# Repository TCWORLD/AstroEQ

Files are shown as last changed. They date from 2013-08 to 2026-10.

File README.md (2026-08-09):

*Last Updated: 8th Aug 2026*

# AstroEQ Telescope Mount Controller

### About The AstroEQ Project

AstroEQ was written and designed by Thomas Carpenter. Assistance with EQMOD and the Skywatcher Protocol was provided by Chris over at the EQMOD Yahoo group.

AstroEQ was primarily designed as an alternative to the SynScan upgrade for Skywatcher telescopes so that I could convert my non-GoTo mount into a full GoTo. Being a EE student at the time I decided to built my own controller rather than buying a commercial one. 

The primary goal of the project was to act as a gateway to connect the excellent EQMOD software (and hence ASCOM planetariums) to a motorised Equatorial mount that previously lacked Goto functionality.

The resulting design allows for almost any equatorial telescope mount which has bipolar stepper motors fitted to the RA and DEC axes to be connected to a PC and controlled via EQMOD.

The AstroEQ code contains a custom developed protocol decoder which uses the same Skywatcher protocol for communication that many Skywatcher go-to mounts use, and the same protocol which EQMOD was developed around. This allows it to be connected to EQMOD without any modification to that software regardless of what type of mount it is.

### Versions

The current software and hardware versions are as follows:

 * Config Utility Version: **3.9.3**
 * Firmware Verison: **8.25**
 * Hardware Version: **4.6/4.7 - see note below**

The AstroEQ configuration utility and precompiled firmware can be downloaded from either the Downloads folder, or the AstroEQ website at: https://astroeq.co.uk/download
Full version history can also be found on the AstroEQ downloads page.

The configuration utility is designed to run natively on Windows or Debian (e.g. Raspian/Ubuntu). You only need to run this utility when programming the mount.

I recommend people use the V4.6 design for DIY controllers.

The new V4.7 hardware design is functionality equivalent to the V4.6 design, but uses a mixture of PTH and SMD components to make it compatible with machine assembly.

### Making your own AstroEQ 

There are two hardware options:

 * Use an Arduino Mega (Uno is not supported), which requires only two DRV8825 or A4988 driver boards and a few passive components to build.
 * Use a completely custom hardware desgin which is based around an Atmega162 chip. Although this is not officially supported by the Arduino IDE, I have modified the bootloader to suit.

Further information can be found at https://astroeq.co.uk/buildown

### Help and Support

If you have any questions or need support, I have opened an AstroEQ Forum which can be found at https://astroeq.co.uk/forum/

The AstroEQ Firmware is currently proving to be very stable. If you do happen across any glitches, let me know as I can usually fix them fairly quickly.

### Required Software

Ascom can be downloaded from their website at: http://ascom-standards.org/ 

The EQMOD Project can be found at: http://eq-mod.sourceforge.net/

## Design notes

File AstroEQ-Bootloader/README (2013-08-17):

If you are building an AstroEQ from scratch, a special bootloader has to be programmed to the Atmega162 IC in order for the configuration utility to be able download the lastest version of the firmware and configure the mount.

The bootloader HEX file is included in this folder.

If you have bought a Kit or ready assembled AstroEQ board directly from me, the bootloader has already been installed. You can skip this step and move on to the config utility.
If you are using an Arduino Mega board, you can also skip this step as they already have a compatible bootloader installed.
If neither of the above apply, please read on...

You will need to connect your programmer to the ISP pins which are shown in the schematic (The ISP header)
You will then need to the software that came with your programmer to download the hex file and set the fuses.

The following fuse settings should be used:

High Fuse: 0xDC
Low Fuse: 0xFF
Extended Fuse*: 0xFB   
(*If you programmer flags up an error on the extended fuse, use 0x1A instead)

I use 'avrdude' to program hex files. You can find a good tutorial for that here: http://www.ladyada.net/learn/avr/avrdude.html

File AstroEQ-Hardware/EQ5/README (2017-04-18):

This is an experimental design I am using for my mount.

It is designed to fit within the shell of a Skywatcher EQ5, though takes a bit of work to install it.

I don't recommend using this design. It is provided as-is without any support.

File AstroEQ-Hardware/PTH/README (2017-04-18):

This folder contains designs used in purchased AstroEQ controllers and PCBs.

Currently V4.6 is the bare PCB version that I sell through the AstroEQ website. It is an easy to solder through-hole board. The Gerber files, Schematic and BOM, as well as the Eagle design files are all available in this folder.

V4.7 is a new part-SMD design that I will be using for the next run of controllers. I have made this switch to allow for machine assembly of the design. I would not recommend building this board yourself as it is functionally identical to the V4.6 board but will not be easy to assemble!

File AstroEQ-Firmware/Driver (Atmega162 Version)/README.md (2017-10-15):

### For Windows 10 Users

Installation of this driver is not necessary.

Windows 10 comes with a compatible driver preinstalled so it should automatically detect and install the necessary driver.

### For Window Vista/7/8.1 Users

Running DPInst_x86 or DPInst_x64 will install the AstroEQ driver (Use _x86 for 32bit OS, or _x64 for 64bit OS).
Alternatively you can install via Device Manager

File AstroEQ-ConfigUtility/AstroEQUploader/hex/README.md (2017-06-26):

Insert latest firmware .hex files here before running.

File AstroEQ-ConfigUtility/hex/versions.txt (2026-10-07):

AstroEQUploaderUtility	3.93
AstroEQV4-DIYBoard(includingKits)	8.29	AstroEQ V4-DIY Board (including DIY)	atmega162	arduino	57600
AstroEQArduinoMega2560	8.29	AstroEQ Arduino Mega 2560	atmega2560	wiring	115200
AstroEQArduinoMega1280	8.29	AstroEQ Arduino Mega 1280	atmega1280	arduino	57600
AstroEQV4-EQ5Board	8.29	AstroEQ V4-EQ5 Board	atmega162	arduino	57600
AstroEQRamps14Mega2560	8.29	AstroEQ Ramps 1.4 w/ Mega 2560	atmega2560	wiring	115200

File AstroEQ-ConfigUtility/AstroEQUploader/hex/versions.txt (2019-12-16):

AstroEQUploaderUtility	3.91
AstroEQV4-DIYBoard(includingKits)	8.16	AstroEQ V4-DIY Board (including DIY)	atmega162	arduino	57600
AstroEQArduinoMega2560	8.16	AstroEQ Arduino Mega 2560	atmega2560	wiring	115200
AstroEQArduinoMega1280	8.16	AstroEQ Arduino Mega 1280	atmega1280	arduino	57600
AstroEQV4-EQ5Board	8.16	AstroEQ V4-EQ5 Board	atmega162	arduino	57600
AstroEQRamps14Mega2560	8.16	AstroEQ Ramps 1.4 w/ Mega 2560	atmega2560	wiring	115200

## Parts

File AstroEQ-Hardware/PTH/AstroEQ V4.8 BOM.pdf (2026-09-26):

Qty | Parts | Value | Description | Manufacturer | Part Number | Farnell Code
| 2 SJ1, SJ2 | - | Solder Jumper - See PCB for details | - | - | -
| 7 C1, C3, C5, C9, C10, C11, C15 | 100nF | 100nF Ceramic Capacitor, 50V, 2.54mm pitch | MULTICOMP | MCRR25104X7RK0050 | 1216438
| 3 C2, C4, C12 | 100uF | 100uF Alu Electrolytic Capacitor, 25V, Dia 6.3mm | MULTICOMP | MCGPR25V107M6.3X11 | 9451188
| 4 C7, C8, C13, C14 | 22pF | 22pF Ceramic Capacitor, 2.54mm pitch | AVX | SR151A220JAR | 1100369
| 1 D1 | MBR1060 | TO-220 Schottky Diode, 10A | MULTICOMP | MBR1060 | 1625119
| 1 ST4 | RJ11-6 | RJ11 JACK, 6/6 LOW PROFILE | MOLEX | 95501-2661 | 1536490
| 2 DEC, RA | RJ11-4 | RJ11 JACK, 6/4 LOW PROFILE | MOLEX | 95501-2641 | 1560166
| 1 HAMMOND-1593N | HAMMOND-1593N | CASE, ABS, HANDHELD, BLACK, 111X75X25MM | HAMMOND | 1593NBK | 9287566
| 1 IC1 | ATMEGA162-16PU | IC, ATMEGA162-16PU, DIP40 | ATMEL | ATMEGA162-16PU | 9171169
| 1 IC1 | DIP40 Socket | 40Way DIP IC Socket, 0.3" Pitch | MULTICOMP | 2227-20-03-07 | 4285608
| 1 IC2 | PIC18F14K50-I/P | IC, PIC18F14K50-I/P, PDIP20 | MICROCHIP | PIC18F14K50-I/P | 1648501
| 1 IC2 | DIP20 Socket | 40Way DIP IC Socket, 0.6" Pitch | MULTICOMP | 2227-40-06-05 | 4285669
| 1 IC3 | 78L05 | 5V 100mA Voltage Regulator, TO-92 | FAIRCHILD SEMICONDUCTOR | LM78L05ACZX | 1467367
| 1 J1 | MJ-179PH | DC Barrel Jack Socket, PCB Mount | MULTICOMP | MJ-179PH | 1737246
| 2 M1, M2 | Motor Driver Socket | RECEPTACLE, 2.54MM, SINGLE, 16WAY | SAMTEC | CES-116-01-T-S | 1667522
| 1 PROG | 2x3 Header | 2ROW, 6WAY, 2.54mm Pitch Header | TE CONNECTIVITY / AMP | 826632-3 | 3418492
7 R13, R14, R15, R16, R19, R21, R23 1kR | 1k Resistor, 1/4W, 5% | MULTICOMP | MF12 1K | 9342400
| 1 USB-> | Mini USB Connector | MINI USB RECEPTACLE, THT, R/A | MOLEX | 565790519 | 1125347
| 1 X2 | 12MHz XTAL | XTAL, 12.000MHZ, 18PF, HC-49S | TXC | 9B-12.000MAAJ-B | 1842203
| 3 R1, R18, R20 | 10kR | 10k Resistor, 1/4W, 5% | MULTICOMP | MF12 10K | 9342419
| 3 PWR, STAT, USB | 3mm LED Red | Flat Top Red LED, 3mm | KINGBRIGHT | L-424HDT | 1142499
| 1 X1 | 16MHz XTAL | XTAL, 16.000MHZ, 18PF, HC-49S | TXC | 9B-16.000MEEJ-B | 1842217
| 1 D2 | 1N4148 | DIODE, 100V,150MA, DO-35 | MULTICOMP | 1N4148 | 9565124
| 1 C6 | 470nF | 470nF Ceramic Capacitor, 50V, 2.54mm pitch | KEMET | C320C474M5U5T
| | | | | A | 1457660
| 1 R22 | 120R | 120R Resistor, 1/4W, 5
| | | % | MULTICOMP | MF12 120R | 9342516
| 1 Q1 | BS270 | MOSFET TRANSISTOR, N CHANNEL, BS270 | FAIRCHILD SEMICONDUCTOR | BS270 | 1017689
| 1 PWM | 3.5mm JACK | PHONE AUDIO CONNECTOR, JACK, 3.5MM | CLIFF ELECTRONIC COMPONENETS | FC68131 | 2518188
1 Pack | - | Mounting PCB to Case | WASHER, FLAT, NYLON, M2.5, PK50 | DURATOOL | 110764 | 7047472
1 Pack | - | Mounting PCB to Case | SCREW, POZI PAN, STEEL, BZP, M2.5X6 | TR FASTENINGS | M2.56 PRSTTTZ100 | 1420119

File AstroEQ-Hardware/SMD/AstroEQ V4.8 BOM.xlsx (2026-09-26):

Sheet: Summary
Number of installed components | 47
Number of different components | 24
Number of BGAs per circuit | 0
Number of QFNs per circuit | 0

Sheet: Parts List Summary
Line No | Part Name | Part Number/Value | Quantity Per Board | REF DES | Notes | Manufacturer | P/N | Supplier | Order Code
1 | POWER_JACKPTH | POWER_JACKPTH | 1 | 12V | . | MULTICOMP | MJ-179PH | Farnell | 1737246
2 | C-EUC0603 | 100n 0603 50V 10% X7R | 7 | C1, C3, C5, C9, C10, C11, C15 | . | MULTICOMP | MC0603B104K500CT | Farnell | 1759122
3 | CPOL-EUD | 100u 0.38R 35V 20% ALU-ELEC | 3 | C2, C4, C12 | . | Wurth Elektronik | 865080545012 | Mouser | 710-865080545012
4 | C-EUC0603 | 470n 0603 16V 10% X5R | 1 | C6 | . | MULTICOMP | MC0603X474K160CT | Farnell | 1759405
5 | C-EUC0603 | 22p 0603 50V 5% C0G/NP0 | 4 | C7, C8, C13, C14 | . | MULTICOMP | MC0603N220J500CT | Farnell | 1759057
6 | DIODE-SMC | B550C-13 SMC | 1 | D1 | . | DIODES INC. | B550C-13-F | Farnell | 1858608
7 | DIODESOD | RB511VM-30FHTE-17 SOD-323 | 1 | D2 | . | ROHM | RB511VM-30FHTE-17 | Farnell | 2581544
8 | RJ11-4-LP | RJ11-4-LP | 2 | DEC, RA | . | Molex | 95501-2641 | Farnell | 1560166
9 | DIP40 | DIP40-SOCKET | 1 | IC1 | . | 3M | 4840-6000-CP | Mouser | 517-4840-6000-CP
10 | DIP20 | DIP20-SOCKET | 1 | IC2 | . | MULTICOMP | 2227-20-03-07 | Farnell | 4285608
11 | V_REG_78XX-SOT89 | 78L05 SOT89 | 1 | IC3 | . | STMicroelectronics | L78L05ACUTR | Farnell | 1366573
12 | LED-1206-SIDE | Red | 3 | LINK, PWR, STAT | . | Wurth Elektronik | 155124RS73200 | Farnell | 2322101
13 | A4983-DUAL-HV | Motor Driver | 2 | M1, M2 | . | Samtec | CES-116-01-T-S | Farnell | 1667522
14 | 2x3-Pin Header | AVR_PRG | 1 | PROG | . | Harwin | M20-9980346 | Farnell | 1022231
15 | AUDIO-JACKPTH | JACK | 1 | PWM | . | CLIFF Electronic Components | FC68131 | Farnell | 2518188
16 | MOSFET-NCHANNELSMD | NTR4501NT1G SOT23 | 1 | Q1 | . | ONSemiconductor | NTR4501NT1G | Farnell | 1431305
17 | R-EU_R0603 | 10k 0603 1% 0.063W | 3 | R1, R18, R20 | . | MULTICOMP | MC0063W0603110K | Farnell | 2130939
18 | R-EU_R0603 | 1k 0603 1% 0.063W | 7 | R13, R14, R15, R16, R19, R21, R23 | . | MULTICOMP | MC0063W060311K | Farnell | 2130855
19 | R-EU_R0805 | 120R 0805 1% 0.1W | 1 | R22 | . | MULTICOMP | MC01W08051120R | Farnell | 2129039
20 | 1x3-Pin Header | 3pin HDR | 2 | SJ1, SJ2 | . | Harwin | M20-9990345 | Farnell | 1022248
21 | RJ11-LP | RJ11-6 | 1 | ST4 | . | Molex | 95501-2661 | Farnell | 1536490
22 | USBMINIAB | Molex 67803-8020 | 1 | USB | . | Molex | 67803-8020 | Farnell | 1355761
23 | XTALNX5032 | 16MHz 5x3.2 20ppm | 1 | X1 | . | ABRACON | ABM3-16.000MHZ-D2Y-T | Mouser | 815-ABM3-16-D2Y-T
24 | XTALNX5032 | 12MHz 5x3.2 30ppm | 1 | X2 | . | TXC | 7A-12.000MAAJ-T | Farnell | 1841940
 |  |  |  |  | .
 |  |  |  |  | .
 |  |  |  |  | .
 |  |  |  |  | .
 |  |  |  |  | .
 |  |  |  |  | .
 |  |  |  |  | .
 |  |  |  |  | .
 |  |  |  |  | .
 |  |  |  |  | .
 |  |  |  |  | .
 |  |  |  |  | .
 |  |  |  |  | .
 |  |  |  |  | .
 |  |  |  |  | .
 |  |  |  |  | .
 |  |  |  |  | .
 |  |  |  |  | .
 |  |  |  |  | .
 |  |  |  |  | .
 |  |  |  |  | .
 |  |  |  |  | .
 |  |  |  |  | .
 |  |  |  |  | .
 |  |  |  |  | .
 |  |  |  |  | .
 |  |  |  |  | .
 |  |  |  |  | .
 |  |  |  |  | .
 |  |  |  |  | .
 |  |  |  |  | .
 |  |  |  |  | .
 |  |  |  |  | .
 |  |  |  |  | .
 |  |  |  |  | .
 |  |  |  |  | .
 |  |  |  |  | .
 |  |  |  |  | .
 |  |  |  |  | .
 |  |  |  |  | .
 |  |  |  |  | .
 |  |  |  |  | .
 |  |  |  |  | .
 |  |  |  |  | .
 |  |  |  |  | .
 |  |  |  |  | .
 |  |  |  |  | .
 |  |  |  |  | .
 |  |  |  |  | .
 |  |  |  |  | .
 |  |  |  |  | .
 |  |  |  |  | .
 |  |  |  |  | .
 |  |  |  |  | .
 |  |  |  |  | .
 |  |  |  |  | .
 |  |  |  |  | .
 |  |  |  |  | .
 |  |  |  |  | .
 |  |  |  |  | .
 |  |  |  |  | .
 |  |  |  |  | .
 |  |  |  |  | .
 |  |  |  |  | .
 |  |  |  |  | .
 |  |  |  |  | .
 |  |  |  |  | .
 |  |  |  |  | .
 |  |  |  |  | .
 |  |  |  |  | .
 |  |  |  |  | .
 |  |  |  |  | .
 |  |  |  |  | .
 |  |  |  |  | .
 |  |  |  |  | .
 |  |  |  |  | .
 |  |  |  |  | .
 |  |  |  |  | .
 |  |  |  |  | .
 |  |  |  |  | .
 |  |  |  |  | .
 |  |  |  |  | .
 |  |  |  |  | .
 |  |  |  |  | .
 |  |  |  |  | .
 |  |  |  |  | .
 |  |  |  |  | .
 |  |  |  |  | .
 |  |  |  |  | .
 |  |  |  |  | .
 |  |  |  |  | .
 |  |  |  |  | .
 |  |  |  |  | .
 |  |  |  |  | .
 |  |  |  |  | .
 |  |  |  |  | .
 |  |  |  |  | .
 |  |  |  |  | .
 |  |  |  |  | .
 |  |  |  |  | .
 |  |  |  |  | .
 |  |  |  |  | .
 |  |  |  |  | .
 |  |  |  |  | .
 |  |  |  |  | .
 |  |  |  |  | .
 |  |  |  |  | .
 |  |  |  |  | .
 |  |  |  |  | .
 |  |  |  |  | .
 |  |  |  |  | .
 |  |  |  |  | .
 |  |  |  |  | .
 |  |  |  |  | .
 |  |  |  |  | .
 |  |  |  |  | .
 |  |  |  |  | .
 |  |  |  |  | .
 |  |  |  |  | .
 |  |  |  |  | .
 |  |  |  |  | .
 |  |  |  |  | .
 |  |  |  |  | .
 |  |  |  |  | .
 |  |  |  |  | .
 |  |  |  |  | .
 |  |  |  |  | .
 |  |  |  |  | .
 |  |  |  |  | .
 |  |  |  |  | .
 |  |  |  |  | .
 |  |  |  |  | .
 |  |  |  |  | .
 |  |  |  |  | .
 |  |  |  |  | .
 |  |  |  |  | .
 |  |  |  |  | .
 |  |  |  |  | .
 |  |  |  |  | .
 |  |  |  |  | .
 |  |  |  |  | .
 |  |  |  |  | .
 |  |  |  |  | .
 |  |  |  |  | .
 |  |  |  |  | .
 |  |  |  |  | .
 |  |  |  |  | .
 |  |  |  |  | .
 |  |  |  |  | .
 |  |  |  |  | .
 |  |  |  |  | .
 |  |  |  |  | .
 |  |  |  |  | .
 |  |  |  |  | .
 |  |  |  |  | .
 |  |  |  |  | .
 |  |  |  |  | .
 |  |  |  |  | .
 |  |  |  |  | .
 |  |  |  |  | .
 |  |  |  |  | .
 |  |  |  |  | .
 |  |  |  |  | .
 |  |  |  |  | .
 |  |  |  |  | .
 |  |  |  |  | .
 |  |  |  |  | .
 |  |  |  |  | .
 |  |  |  |  | .
 |  |  |  |  | .
 |  |  |  |  | .
 |  |  |  |  | .
 |  |  |  |  | .
 |  |  |  |  | .
 |  |  |  |  | .
 |  |  |  |  | .
 |  |  |  |  | .
 |  |  |  |  | .
 |  |  |  |  | .
 |  |  |  |  | .
 |  |  |  |  | .
 |  |  |  |  | .
 |  |  |  |  | .
 |  |  |  |  | .
 |  |  |  |  | .
 |  |  |  |  | .
 |  |  |  |  | .
 |  |  |  |  | .
 |  |  |  |  | .
 |  |  |  |  | .
 |  |  |  |  | .
 |  |  |  |  | .
 |  |  |  |  | .
 |  |  |  |  | .
 |  |  |  |  | .
 |  |  |  |  | .
 |  |  |  |  | .
 |  |  |  |  | .
 |  |  |  |  | .
 |  |  |  |  | .
 |  |  |  |  | .
 |  |  |  |  | .
 |  |  |  |  | .
 |  |  |  |  | .
 |  |  |  |  | .
 |  |  |  |  | .
 |  |  |  |  | .
 |  |  |  |  | .
 |  |  |  |  | .
 |  |  |  |  | .
 |  |  |  |  | .
 |  |  |  |  | .
 |  |  |  |  | .
 |  |  |  |  | .
 |  |  |  |  | .
 |  |  |  |  | .
 |  |  |  |  | .
 |  |  |  |  | .
 |  |  |  |  | .
 |  |  |  |  | .
 |  |  |  |  | .
 |  |  |  |  | .
 |  |  |  |  | .
 |  |  |  |  | .
 |  |  |  |  | .
 |  |  |  |  | .
 |  |  |  |  | .
 |  |  |  |  | .
 |  |  |  |  | .
 |  |  |  |  | .
 |  |  |  |  | .
 |  |  |  |  | .
 |  |  |  |  | .
 |  |  |  |  | .
 |  |  |  |  | .
 |  |  |  |  | .
 |  |  |  |  | .

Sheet: Master BOM
Ref Designator | Part Name | BOM Value | Rotation | X (thou) | Y (thou) | Side | Part ID | Line No | Install? | Is BGA | Is QFN | Manufacturer | Manufacturers P/N
12V | POWER_JACKPTH | POWER_JACKPTH | 270 | -2.22 | 47.31 | TOP | 40 | 1 | TRUE | FALSE | FALSE | MULTICOMP | MJ-179PH
C1 | C-EUC0603 | 100n 0603 50V 10% X7R | 270 | 80.01 | 15.24 | TOP | 13 | 2 | TRUE | FALSE | FALSE | MULTICOMP | MC0603B104K500CT
C3 | C-EUC0603 | 100n 0603 50V 10% X7R | 270 | 80.01 | 35.56 | TOP | 13 | 2 | TRUE | FALSE | FALSE | MULTICOMP | MC0603B104K500CT
C5 | C-EUC0603 | 100n 0603 50V 10% X7R | 180 | 17.46 | 14.29 | TOP | 13 | 2 | TRUE | FALSE | FALSE | MULTICOMP | MC0603B104K500CT
C9 | C-EUC0603 | 100n 0603 50V 10% X7R | 0 | 23.5 | 37.47 | TOP | 13 | 2 | TRUE | FALSE | FALSE | MULTICOMP | MC0603B104K500CT
C10 | C-EUC0603 | 100n 0603 50V 10% X7R | 180 | 11.11 | 64.45 | TOP | 13 | 2 | TRUE | FALSE | FALSE | MULTICOMP | MC0603B104K500CT
C11 | C-EUC0603 | 100n 0603 50V 10% X7R | 0 | 6.03 | 58.42 | TOP | 13 | 2 | TRUE | FALSE | FALSE | MULTICOMP | MC0603B104K500CT
C15 | C-EUC0603 | 100n 0603 50V 10% X7R | 180 | 26.67 | 3.81 | TOP | 13 | 2 | TRUE | FALSE | FALSE | MULTICOMP | MC0603B104K500CT
C2 | CPOL-EUD | 100u 0.38R 35V 20% ALU-ELEC | 90 | 82.87 | 29.85 | TOP | 15 | 3 | TRUE | FALSE | FALSE | Wurth Elektronik | 865080545012
C4 | CPOL-EUD | 100u 0.38R 35V 20% ALU-ELEC | 90 | 82.87 | 48.58 | TOP | 15 | 3 | TRUE | FALSE | FALSE | Wurth Elektronik | 865080545012
C12 | CPOL-EUD | 100u 0.38R 35V 20% ALU-ELEC | 180 | 18.73 | 51.12 | TOP | 15 | 3 | TRUE | FALSE | FALSE | Wurth Elektronik | 865080545012
C6 | C-EUC0603 | 470n 0603 16V 10% X5R | 0 | 9.21 | 25.08 | TOP | 14 | 4 | TRUE | FALSE | FALSE | MULTICOMP | MC0603X474K160CT
C7 | C-EUC0603 | 22p 0603 50V 5% C0G/NP0 | 270 | 24.77 | 9.53 | TOP | 12 | 5 | TRUE | FALSE | FALSE | MULTICOMP | MC0603N220J500CT
C8 | C-EUC0603 | 22p 0603 50V 5% C0G/NP0 | 270 | 20.32 | 9.53 | TOP | 12 | 5 | TRUE | FALSE | FALSE | MULTICOMP | MC0603N220J500CT
C13 | C-EUC0603 | 22p 0603 50V 5% C0G/NP0 | 0 | 53.66 | 47.31 | TOP | 12 | 5 | TRUE | FALSE | FALSE | MULTICOMP | MC0603N220J500CT
C14 | C-EUC0603 | 22p 0603 50V 5% C0G/NP0 | 0 | 53.66 | 44.13 | TOP | 12 | 5 | TRUE | FALSE | FALSE | MULTICOMP | MC0603N220J500CT
D1 | DIODE-SMC | B550C-13 SMC | 180 | 20.96 | 59.69 | TOP | 24 | 6 | TRUE | FALSE | FALSE | DIODES INC. | B550C-13-F
D2 | DIODESOD | RB511VM-30FHTE-17 SOD-323 | 180 | 9.21 | 22.86 | TOP | 23 | 7 | TRUE | FALSE | FALSE | ROHM | RB511VM-30FHTE-17
DEC | RJ11-4-LP | RJ11-4-LP | 90 | 96.84 | 43.82 | TOP | 33 | 8 | TRUE | FALSE | FALSE | Molex | 95501-2641
RA | RJ11-4-LP | RJ11-4-LP | 90 | 96.84 | 23.5 | TOP | 33 | 8 | TRUE | FALSE | FALSE | Molex | 95501-2641
IC1 | DIP40 | DIP40-SOCKET | 90 | 37.47 | 27.94 | TOP | 35 | 9 | TRUE | FALSE | FALSE | 3M | 4840-6000-CP
IC2 | DIP20 | DIP20-SOCKET | 180 | 16.51 | 28.58 | TOP | 34 | 10 | TRUE | FALSE | FALSE | MULTICOMP | 2227-20-03-07
IC3 | V_REG_78XX-SOT89 | 78L05 SOT89 | 0 | 6.67 | 62.23 | TOP | 22 | 11 | TRUE | FALSE | FALSE | STMicroelectronics | L78L05ACUTR
LINK | LED-1206-SIDE | Red | 90 | 1.38 | 29.85 | TOP | 26 | 12 | TRUE | FALSE | FALSE | Wurth Elektronik | 155124RS73200
PWR | LED-1206-SIDE | Red | 90 | 1.38 | 55.25 | TOP | 26 | 12 | TRUE | FALSE | FALSE | Wurth Elektronik | 155124RS73200
STAT | LED-1206-SIDE | Red | 90 | 1.38 | 4.13 | TOP | 26 | 12 | TRUE | FALSE | FALSE | Wurth Elektronik | 155124RS73200
M1 | A4983-DUAL-HV | Motor Driver | 270 | 77.47 | 32.38 | TOP | 36 | 13 | TRUE | FALSE | FALSE | Samtec | CES-116-01-T-S
M2 | A4983-DUAL-HV | Motor Driver | 270 | 64.77 | 32.38 | TOP | 36 | 13 | TRUE | FALSE | FALSE | Samtec | CES-116-01-T-S
PROG | 2x3-Pin Header | AVR_PRG | 270 | 50.48 | 27.3 | TOP | 38 | 14 | TRUE | FALSE | FALSE | Harwin | M20-9980346
PWM | AUDIO-JACKPTH | JACK | 180 | 97.47 | 59.05 | TOP | 39 | 15 | TRUE | FALSE | FALSE | CLIFF Electronic Components | FC68131
Q1 | MOSFET-NCHANNELSMD | NTR4501NT1G SOT23 | 270 | 87.95 | 55.25 | TOP | 25 | 16 | TRUE | FALSE | FALSE | ONSemiconductor | NTR4501NT1G
R1 | R-EU_R0603 | 10k 0603 1% 0.063W | 270 | 22.86 | 34.93 | TOP | 19 | 17 | TRUE | FALSE | FALSE | MULTICOMP | MC0063W0603110K
R18 | R-EU_R0603 | 10k 0603 1% 0.063W | 270 | 22.86 | 24.13 | TOP | 19 | 17 | TRUE | FALSE | FALSE | MULTICOMP | MC0063W0603110K
R20 | R-EU_R0603 | 10k 0603 1% 0.063W | 270 | 26.35 | 36.51 | TOP | 19 | 17 | TRUE | FALSE | FALSE | MULTICOMP | MC0063W0603110K
R13 | R-EU_R0603 | 1k 0603 1% 0.063W | 180 | 4.45 | 5.71 | TOP | 17 | 18 | TRUE | FALSE | FALSE | MULTICOMP | MC0063W060311K
R14 | R-EU_R0603 | 1k 0603 1% 0.063W | 180 | 4.45 | 56.2 | TOP | 17 | 18 | TRUE | FALSE | FALSE | MULTICOMP | MC0063W060311K
R15 | R-EU_R0603 | 1k 0603 1% 0.063W | 180 | 23.5 | 40.01 | TOP | 17 | 18 | TRUE | FALSE | FALSE | MULTICOMP | MC0063W060311K
R16 | R-EU_R0603 | 1k 0603 1% 0.063W | 180 | 23.5 | 42.55 | TOP | 17 | 18 | TRUE | FALSE | FALSE | MULTICOMP | MC0063W060311K
R19 | R-EU_R0603 | 1k 0603 1% 0.063W | 0 | 9.21 | 27.3 | TOP | 17 | 18 | TRUE | FALSE | FALSE | MULTICOMP | MC0063W060311K
R21 | R-EU_R0603 | 1k 0603 1% 0.063W | 270 | 27.62 | 27.94 | TOP | 17 | 18 | TRUE | FALSE | FALSE | MULTICOMP | MC0063W060311K
R22 | R-EU_R0805 | 120R 0805 1% 0.1W | 180 | 87.95 | 52.39 | TOP | 20 | 19 | TRUE | FALSE | FALSE | MULTICOMP | MC01W08051120R
SJ1 | 1x3-Pin Header | 3pin HDR | 270 | 61.6 | 47.62 | TOP | 37 | 20 | TRUE | FALSE | FALSE | Harwin | M20-9990345
SJ2 | 1x3-Pin Header | 3pin HDR | 270 | 61.6 | 27.3 | TOP | 37 | 20 | TRUE | FALSE | FALSE | Harwin | M20-9990345
ST4 | RJ11-LP | RJ11-6 | 90 | 96.84 | 7.3 | TOP | 32 | 21 | TRUE | FALSE | FALSE | Molex | 95501-2661
USB | USBMINIAB | Molex 67803-8020 | 270 | 4 | 13.97 | TOP | 31 | 22 | TRUE | FALSE | FALSE | Molex | 67803-8020
X1 | XTALNX5032 | 16MHz 5x3.2 20ppm | 270 | 49.85 | 45.72 | TOP | 29 | 23 | TRUE | FALSE | FALSE | ABRACON | ABM3-16.000MHZ-D2Y-T
X2 | XTALNX5032 | 12MHz 5x3.2 30ppm | 0 | 22.54 | 13.34 | TOP | 28 | 24 | TRUE | FALSE | FALSE | TXC | 7A-12.000MAAJ-T
GPIO | M05PTH | -- -- -- -- -- -- | 90 | 25.4 | 27.94 | TOP | 3 |  | FALSE | FALSE | FALSE | -- | --
HAMMOND-1593N | HAMMOND-1593N-4HOLE | -- -- -- -- -- -- | 0 | 0 | 0 | TOP | 3 |  | FALSE | FALSE | FALSE | -- | --
ICL1 | IC | -- -- -- -- -- -- | 180 | 37.47 | 45.72 | TOP | 3 |  | FALSE | FALSE | FALSE | -- | --
ICL2 | IC | -- -- -- -- -- -- | 180 | 16.51 | 28.58 | TOP | 3 |  | FALSE | FALSE | FALSE | -- | --
J2 | JUMPER | -- -- -- -- -- -- | 0 | 61.6 | 28.58 | TOP | 3 |  | FALSE | FALSE | FALSE | -- | --
J3 | JUMPER | -- -- -- -- -- -- | 0 | 61.6 | 48.9 | TOP | 3 |  | FALSE | FALSE | FALSE | -- | --
LOGO1 | ASTROEQ5MM | -- -- -- -- -- -- | 0 | 61.6 | 59.69 | TOP | 3 |  | FALSE | FALSE | FALSE | -- | --

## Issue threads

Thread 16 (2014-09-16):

Microstepping using spiral search

N-DD, 2014-09-16:
Hi!

I installed AstroEQ on an Arduino Mega2560 and I am using it to control two steppers with 200 steps/rev, 16x micro stepping, 1:10 reduction, 1:144 worm reduction. Due to Pin18 being dead on my board I changed PinMappings.h (and wired the DEC stepper driver accordingly) as following:

``` c
#define modePins0_0_Define 15
#define modePins1_0_Define 16
#define modePins2_0_Define 17
#define modePins0_1_Define 21//20
#define modePins1_1_Define 20//19
#define modePins2_1_Define 19//18
```

I then uploaded the modified Arduino sketch and using the config utility I set a maximum slew speed of 144x sidereal rate: according to what I have read, the system should always use 16x micro stepping (speed is always <200x sidereal). However, I noticed that when using the "spiral search" feature of EQMOD, the motors seem to run at 2x micro stepping, and also after a slew there is a small "correction" done at 2x. Is this a normal behavior?

Thanks,

Nico

TCWORLD, 2017-02-12:
Once the V7.5 firmware is released (currently in beta on the AstroEQ forum), the option to disable high torque go-to movements is now merged and selectable from the config utility.

It is not possible to set a different go-to speed for the corrections because as far as the AstroEQ is concerned there is no way to tell them apart from normal go-to movements. However due to the option to disable high torque now being present in the config utility, the go-to speed is now calculated to account for high torque being disabled, so you may be able to go faster.

Once the beta testing is done and the v7.5-dev branch merged, I hope to close this issue. If you continue to have problems you can reopen it.

Closed 2017-04-18.

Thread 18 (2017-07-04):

Cannot register to AstroEQ forum

gnthibault, 2017-07-04:
Hi

First, I would like to thank you for all the work

I am sorry that I use this github issue channel to contact you, but unfortunately, my AstroEQ forum registration is still pending for approval after a few days.
When I go the website : https://www.astroeq.co.uk/forum/ it looks like I cannot login.
I am thinking about ordering a AstroEQ, but I wanted to now if it would be easy to modify the card so that I can use my current connectors (old AT keyboard connector) by soldering the wires directly on the board.

Thank you in advance, and thank you again for your work on AstroEQ

Closed 2017-07-18.

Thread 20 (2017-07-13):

[Arduino Mega] V8.04 EEPROM read failed

cisforcer, 2017-07-13:
mega2560
but  good with v7.4

TCWORLD, 2017-07-18:
Are you using the latest version of the configuration utility? Only the latest version of the config utility will work with the new firmware due to internal changes.

TCWORLD, 2017-07-18:
Found the issue. Bear with me.

TCWORLD, 2017-07-18:
Having solved one part of the problem, there is still a glitch in the Atmega2560 version of the firmware. I'm still looking.

TCWORLD, 2017-07-18:
The issue should now be resolved. If not you can reopen and I'll look further.

cisforcer, 2017-07-25:
HI   @TCWORLD   i just run   8.05 configuration gui and reading  the eeprom  . you are  awesome!!

Closed 2017-07-18.

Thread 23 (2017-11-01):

GUI-related bug in the utility

SquareBoot, 2017-11-01:
Hello,
I'm new to AstroEQ, so I haven't built / bought it yet. However, I tried to install the "AstroEQ Firmware Update Utility V3.7.3" on my Kubuntu 17.04 computer using the latest deb installer available. It seem to work fine, although I can't, obviously, select a device. I want to report the following bug: whenever I try to maximize the window it starts to blink, as the screenshot shows.

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

Something similar happens if I try to resize the window horizontally. I know that the utility has been written in Processing 3, so it may be a Processing or ControlP5 lib bug (but I'm not a Processing developer, so I'm not able to debug it).
`java -version`:

> java version "1.8.0_151"
Java(TM) SE Runtime Environment (build 1.8.0_151-b12)
Java HotSpot(TM) 64-Bit Server VM (build 25.151-b12, mixed mode)

Output of the Processing IDE:

> No library found for processing.awt.PSurfaceAWT
Starting AstroEQ Config Utility, V3.8.0
Time is 21:36:13
OS: Linux. JRE Version: 1.8.0_144. JRE Arch: amd64
Creating Window. Setting DPI Scaling to 1
Setting Window Size to: 510 x 520
Setting Frame Rate
Creating Executioner thread
Connecting to Clipboard
Current Dir: /usr/share/doc/astroequploader/
Loading ControlP5
ControlP5 2.2.6 infos, comments, questions at http://www.sojamo.de/libraries/controlP5
Building GUI
x=0, y=104, width=510, height=352
buildBeginScreen --- ID is: begin
buildVersionCheckScreen --- ID is: versionCheck
buildFirmwareFetchScreen --- ID is: firmwareFetch
buildEEPROMWriterScreen --- ID is: EEPROMWriter
buildCheckEEPROMScreen --- ID is: checkEEPROM
buildRecoverEEPROMScreen --- ID is: recoverEEPROM
buildEnterConfigScreen --- ID is: enterConfig
buildProgramConfigScreen --- ID is: programConfig
buildDownloadFirmwareScreen --- ID is: downloadFirmware
buildTestFirmwareScreen --- ID is: testFirmware
buildFinishedScreen --- ID is: finished
Board Version: AstroEQV4-DIYBoard(includingKits)
Matched to firmware file: AstroEQV4-DIYBoard(includingKits).hex
Initialising Serial Ports
/dev/ttyS0 /dev/ttyS1 /dev/ttyS2 /dev/ttyS3 /dev/ttyS4 /dev/ttyS5 /dev/ttyS6 /dev/ttyS7 /dev/ttyS8 /dev/ttyS9 /dev/ttyS10 /dev/ttyS11 /dev/ttyS12 /dev/ttyS13 /dev/ttyS14 /dev/ttyS15 /dev/ttyS16 /dev/ttyS17 /dev/ttyS18 /dev/ttyS19 /dev/ttyS20 /dev/ttyS21 /dev/ttyS22 /dev/ttyS23 /dev/ttyS24 /dev/ttyS25 /dev/ttyS26 /dev/ttyS27 /dev/ttyS28 /dev/ttyS29 /dev/ttyS30 /dev/ttyS31
Matched to firmware file: AstroEQV4-DIYBoard(includingKits).hex
JFW:524 JFWO:8
JFW:578 JFWO:8
JFW:667 JFWO:8
JFW:696 JFWO:8
JFW:696 JFWO:8
IB:520 JFH:730 JFHO:33
JFW:1374 JFWO:8
JFW:1374 JFWO:8

I hope this helps.
Thanks,
SquareBoot

P.S.: why don't you move the utility to Java, better if using a GUI builder like IntelliJ's one? As far as I know, it hasn't got similar bugs.

TCWORLD, 2017-11-01:
Hi,

The utility isn't meant to be maximised, nor does it need to be. It's really not designed to be resized other than vertically. So the workaround is simply don't maximise the window.

It was written in a hurry some years ago to get away from having to use command line and excel spreadsheets for the configuration. Moreover it was intended for Windows, and then essentially tweaked and patched to get it to run natively on Linux.

The whole thing is not well written and could use a complete overhaul, but given that it does what it needs to do which is to get the configuration on to the controller, it isn't worth the time it would take to completely redesign it.

The source is available, so you are more than welcome to have a go at building a better GUI (bearing in mind whatever is made must be compatible with Windows), and I can provide guidance as to the lower level parts if needed.

Kind Regards,
Tom.

SquareBoot, 2017-11-02:
Thanks for your reply!
By the way, can the firmware be run on an Arduino Due instead of Mega 2560 without modifications?
SquareBoot

TCWORLD, 2017-11-02:
No, the Arduino Due is an entirely different architecture (ARM), and in no way supported. It would require a massive amount of low level assembly rewrite to support it.

SquareBoot, 2017-11-02:
OK, thanks again. I'll close this report.
SquareBoot

Closed 2017-11-02.

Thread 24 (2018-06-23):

AstroEQ doesn't work with EQMOD 2.xx

petrilakm, 2018-06-23:
EQMOD send to device on initialisation commands ":O10" fillowed by ":O11". Because you use "O" as progmode select command, AstroEQ is switched to programmin mode and stop responding to normal commands. EQMOD then hangs-up.
Solution is to move "progmode" command to other letter as "O".

TCWORLD, 2018-06-23:
Which version of EQMOD?

I've not ever seen EQMOD send the :O command, and have never had the problem you describe. Could you provide more details.

petrilakm, 2018-06-23:
EQASCOM_V200k
Also there is listed "O" as standart Sky-watcher commad:
https://github.com/skywatcher-pacific/skywatcher_open/wiki/Skywatcher-Protocol

I haven't original synscan, so I know only information published on web.

TCWORLD, 2018-06-23:
Interesting.

Seems there have been some changes to EQMOD since AstroEQ was first developed, and new commands added by Skywatcher.

I'm looking in to the issue.

TCWORLD, 2018-06-23:
I've pushed a new version of the config utility and firmware.

I believe this should solve the issue - seems to on my end.

TCWORLD, 2018-06-30:
I believe this is now resolved. If it's not, feel free to reopen.

jgwood, 2018-09-17:
Hi Tom
I have packaged my controller and will send off today by Royal Mail , I have included a note of drive setup etc, just hope you can resolve the time out in EQMod test after configuration.
Thank you again.
Jim Wood.

Sent from my iPhone

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

Closed 2018-06-30.

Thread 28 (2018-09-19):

Strange design of the Arduino version

Violin9906, 2018-09-19:
I recognized that the power source is directly connected with the Arduino VIN. And that caused my LP2985 on Arduino board burnd.

Closed 2018-10-27.

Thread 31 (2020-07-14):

Config utility doesn't start with Java >=10

marcocipriani01, 2020-07-14:
The config utility doesn't start with Java 14 (or any other JDK/JRE >=10). In Windows 10 it states that Java 1.8.0 isn't installed, while on Ubuntu 20.04 it says that "the installed Java version isn't valid". Java is of course in the PATH env var on both my Ubuntu and Windows installations.
Probably it doesn't expect the Java version to be X.y.z (with X the major version number) but rather 1.X.y (indeed, Java 8 used to report himself as 1.8.0)

```
C:\>java.exe -version

java version "14.0.1" 2020-04-14
Java(TM) SE Runtime Environment (build 14.0.1+7)
Java HotSpot(TM) 64-Bit Server VM (build 14.0.1+7, mixed mode, sharing)
```

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

TCWORLD, 2020-07-14:
Could you try the following verion on Windows. I'm still looking into Ubuntu.

The config utility was designed for Java 8, so I have no idea if it will work on Java 14, but I've updated the version of launch4j which should now handle the new version numbers and realise that 14.0.1 is newer than 1.8.0.

[AstroEQ-ConfigUtility.zip](https://github.com/TCWORLD/AstroEQ/files/4918327/AstroEQ-ConfigUtility.zip)

TCWORLD, 2020-07-14:
For Ubuntu, could you run the following script:

```
#!/bin/sh
JAVA_VER=$(java -version 2>&1 | sed 's/.*version "\(.*\)\.\(.*\)\..*"/\1\2/; 1q')
[ "$JAVA_VER" -ge 18 ] && echo "ok, java is 1.8 or newer" || echo "it's too old..."
```

marcocipriani01, 2020-07-14:
On Windows I only get the loading screen, while the config utility is all grey, nothing is drawn

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

marcocipriani01, 2020-07-14:
Linux:

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

TCWORLD, 2020-07-14:
Could you extract this into the same folder as AstroEQ.exe and run it.
[AstroEQDebug.zip](https://github.com/TCWORLD/AstroEQ/files/4918406/AstroEQDebug.zip)

It will run AstroEQ with a command prompt to provide debugging information.

marcocipriani01, 2020-07-14:
Here you go
```
Starting AstroEQ Config Utility, V3.9.2
Time is 13:20:58
OS: Windows 10. JRE Version: 14.0.1. JRE Arch: amd64
Java Path: D:\Windows\Programs\JDK14\bin;C:\WINDOWS\Sun\Java\bin;C:\WINDOWS\system32;C:\WINDOWS;C:\Program Files (x86)\Intel\iCLS Client\;C:\Program Files\Intel\iCLS Client\;C:\windows\system32;C:\windows;C:\windows\System32\Wbem;C:\windows\System32\WindowsPowerShell\v1.0\;C:\Program Files (x86)\Intel\Intel(R) Management Engine Components\DAL;C:\Program Files\Intel\Intel(R) Management Engine Components\DAL;C:\Program Files (x86)\Intel\Intel(R) Management Engine Components\IPT;C:\Program Files\Intel\Intel(R) Management Engine Components\IPT;C:\Program Files (x86)\NVIDIA Corporation\PhysX\Common;C:\WINDOWS\system32;C:\WINDOWS;C:\WINDOWS\System32\Wbem;C:\WINDOWS\System32\WindowsPowerShell\v1.0\;C:\WINDOWS\System32\OpenSSH\;C:\Program Files\Intel\WiFi\bin\;C:\Program Files\Common Files\Intel\WirelessCommon\;C:\Program Files\NVIDIA Corporation\NVIDIA NvDLISR;C:\WINDOWS\system32;C:\WINDOWS;C:\WINDOWS\System32\Wbem;C:\WINDOWS\System32\WindowsPowerShell\v1.0\;C:\WINDOWS\System32\OpenSSH\;C:\Program Files\Microsoft SQL Server\120\Tools\Binn\;D:\Windows\Programs\Git\cmd;C:\Users\marco\AppData\Local\Microsoft\WindowsApps;C:\Users\marco\AppData\Local\GitHubDesktop\bin;C:\Users\marco\AppData\Local\Microsoft\WindowsApps;C:\Program Files\Intel\WiFi\bin\;C:\Program Files\Common Files\Intel\WirelessCommon\;;D:\Windows\Programs\Microsoft VS Code\bin;D:\Windows\Programs\JDK14\bin;.
Creating Window. Setting DPI Scaling to 1
Setting Window Size to: 510 x 525
Setting Frame Rate
Creating Executioner thread
Connecting to Clipboard
java.lang.UnsatisfiedLinkError: C:\Users\marco\Desktop\AstroEQ-ConfigUtility\bin\jSSC-2.8.dll: Can't load IA 32-bit .dll on a AMD 64-bit platform
        at java.base/java.lang.ClassLoader$NativeLibrary.load0(Native Method)
        at java.base/java.lang.ClassLoader$NativeLibrary.load(ClassLoader.java:2452)
        at java.base/java.lang.ClassLoader$NativeLibrary.loadLibrary(ClassLoader.java:2508)
        at java.base/java.lang.ClassLoader.loadLibrary0(ClassLoader.java:2704)
        at java.base/java.lang.ClassLoader.loadLibrary(ClassLoader.java:2669)
        at java.base/java.lang.Runtime.loadLibrary0(Runtime.java:807)
        at java.base/java.lang.System.loadLibrary(System.java:1907)
        at AstroEQUploader.setup(AstroEQUploader.java:231)
        at processing.core.PApplet.handleDraw(PApplet.java:2393)
        at processing.awt.PSurfaceAWT$12.callDraw(PSurfaceAWT.java:1540)
        at processing.core.PSurfaceNone$AnimationThread.run(PSurfaceNone.java:316)
Current Dir: C:/Users/marco/Desktop/AstroEQ-ConfigUtility/AstroEQDebug.exe\
Populating Firmware Variants
The file "C:/Users/marco/Desktop/AstroEQ-ConfigUtility/AstroEQDebug.exe\hex\versions.txt" is missing or inaccessible, make sure the URL is valid or that the file has been added to your sketch and is readable.
java.lang.NullPointerException
        at java.base/java.io.Reader.<init>(Reader.java:167)
        at java.base/java.io.BufferedReader.<init>(BufferedReader.java:101)
        at java.base/java.io.BufferedReader.<init>(BufferedReader.java:116)
        at AstroEQUploader.populateVariants(AstroEQUploader.java:432)
        at AstroEQUploader.setup(AstroEQUploader.java:267)
        at processing.core.PApplet.handleDraw(PApplet.java:2393)
        at processing.awt.PSurfaceAWT$12.callDraw(PSurfaceAWT.java:1540)
        at processing.core.PSurfaceNone$AnimationThread.run(PSurfaceNone.java:316)
Board List Loaded
Loading ControlP5
ControlP5 2.2.6 infos, comments, questions at http://www.sojamo.de/libraries/controlP5
Building GUI
x=0, y=104, width=510, height=372
buildBeginScreen --- ID is: begin
buildVersionCheckScreen --- ID is: versionCheck
buildFirmwareFetchScreen --- ID is: firmwareFetch
buildEEPROMWriterScreen --- ID is: EEPROMWriter
buildCheckEEPROMScreen --- ID is: checkEEPROM
buildRecoverEEPROMScreen --- ID is: recoverEEPROM
buildEnterConfigScreen --- ID is: enterConfig
buildProgramConfigScreen --- ID is: programConfig
buildDownloadFirmwareScreen --- ID is: downloadFirmware
buildTestFirmwareScreen --- ID is: testFirmware
buildFinishedScreen --- ID is: finished
Initialising Serial Ports
java.lang.UnsatisfiedLinkError: 'java.lang.String[] jssc.SerialNativeInterface.getSerialPortNames()'
        at jssc.SerialNativeInterface.getSerialPortNames(Native Method)
        at jssc.SerialPortList.getWindowsPortNames(SerialPortList.java:309)
        at jssc.SerialPortList.getPortNames(SerialPortList.java:298)
        at jssc.SerialPortList.getPortNames(SerialPortList.java:182)
        at processing.serial.Serial.list(Unknown Source)
        at AstroEQUploader.refreshComm(AstroEQUploader.java:303)
        at AstroEQUploader.setup(AstroEQUploader.java:293)
        at processing.core.PApplet.handleDraw(PApplet.java:2393)
        at processing.awt.PSurfaceAWT$12.callDraw(PSurfaceAWT.java:1540)
        at processing.core.PSurfaceNone$AnimationThread.run(PSurfaceNone.java:316)
```

TCWORLD, 2020-07-14:
Ok, so that makes some sense.

The Config utility only supports 32-bit Java, so you'll need to have the 32bit JRE installed. Otherwise the JSSC DLL for serial comms won't load correctly.

---

For Ubuntu, what does this return:

```
#!/bin/sh

#https://stackoverflow.com/a/56243046/1557472
JAVA_VER=$(java -version 2>&1 | head -1 | cut -d'"' -f2 | sed '/^1\./s///' | cut -d'.' -f1)

[ "$JAVA_VER" -ge 8 ] && echo "ok, java is 1.8 or newer" || echo "it's too old..."

```

marcocipriani01, 2020-07-14:
Debugging from Processing does work, but ofc reports it lacks a 64-bit jSSC library. I'll give you a compatible DLL in a moment.

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

New script:

```
marco@marco-win:/tmp$ ./test2
ok, java is 1.8 or newer
```

TCWORLD, 2020-07-14:
I've got a copy of the 64 bit DLL, its a case of trying to figure out whether I can load it based on architecture. Last time I tried it got upset because the name didn't match.

---

For the ubuntu, could you modify `/usr/bin/astroequploader` (just a script file) and change lines 11 and 12 from:

```
JAVA_VER=$(java -version 2>&1 | sed 's/.*version "\(.*\)\.\(.*\)\..*"/\1\2/; 1q$
if [ "$JAVA_VER" -lt 18 ]; then
```

to;

```
#https://stackoverflow.com/a/56243046/1557472
JAVA_VER=$(java -version 2>&1 | head -1 | cut -d'"' -f2 | sed '/^1\./s///' | cut -d'.' -f1)
if [ "$JAVA_VER" -lt 8 ]; then
```

And see if that launches.

marcocipriani01, 2020-07-14:
I'm taking a look at the sources, and I understand why you got upset. You should use the jSSC jar library (which automatically selects the right DLL) instead of the DLLs directly. But that would mean rewriting part of the config utility, perhaps in pure Java. I'll test the new Ubuntu launcher ASAP.

TCWORLD, 2020-07-14:
It is using the jar library, the problem is that in order to wrap everything in a single EXE I have to merge all of the jars into a single fat jar, at which point the JSSC jar file seemed unable or unwilling to load the DLL. There seems to be some weird path issue that I never sussed.

The config utility is a bit of a mess - was written in a hurry, I've just never had the time to tidy it up.

TCWORLD, 2020-07-14:
Hmm. In fact it seems to be working without loading the DLL. Interesting.

TCWORLD, 2020-07-14:
New version to try out if you could

[AstroEQDebug.zip](https://github.com/TCWORLD/AstroEQ/files/4918598/AstroEQDebug.zip)

TCWORLD, 2020-07-14:
Never mind, it does need the DLL. Must be finding it on my Path somewhere.

marcocipriani01, 2020-07-14:
AstroEQ-ConfigUtility-LINUX.zip works every once in a while, I have to open it several times before getting an usable GUI. Most of the times launches a gray window or no window at all.

Output of the new Windows Debug exe (still gray window):
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
TCWORLD, 2020-07-14:
Take 4 - this seems to load the DLL properly when it has a different name. I've called one jSSC-2.6-x86 and the other jSSC-2.6-amd64. Hopefully that should load for you.

[AstroEQDebug.zip](https://github.com/TCWORLD/AstroEQ/files/4918764/AstroEQDebug.zip)

There is still a strange issue with the sketch path that I'm trying to figure out. This may fix that too.

Not sure about ubuntu yet. Still looking.

marcocipriani01, 2020-07-14:
I'm sorry, go for take 5 😄 now the GUI loads and responses, but as soon as I connect an AstroEQ V4.7 board and hit Configure it crashes the bad way with a Java EXCEPTION_ACCESS_VIOLATION. Error log: [hs_err_pid9400.log](https://github.com/TCWORLD/AstroEQ/files/4918849/hs_err_pid9400.log)

TCWORLD, 2020-07-14:
Lol. That seems to be an issue with the 64bit version of JSSC itself. At least its loading the correct DLL now.

----

Meanwhile, this seems to fix Ubuntu for me - loads and talks to the AstroEQ:

[AstroEQ-ConfigUtility-LINUX.zip](https://github.com/TCWORLD/AstroEQ/files/4918933/AstroEQ-ConfigUtility-LINUX.zip)

Occasionally it will load with a black screen, at which point resizing the window brings it back. Not sure what that is about.

TCWORLD, 2020-07-14:
Theres a newer version of JSSC here: https://github.com/java-native/jssc/releases/tag/v2.9.1

Downloading the native library from there and renaming it to 2.8 seems to still work for the x86 version. I've attached the amd64 native from there. Might be worth a try.

[jSSC-2.8-amd64.zip](https://github.com/TCWORLD/AstroEQ/files/4918972/jSSC-2.8-amd64.zip)

marcocipriani01, 2020-07-14:
The latest linux version loads, but I'm running it in a virtual machine, so I can't test if it connects to the board. I'll switch to my full Ubuntu installation when I reboot the PC. jSSC 2.9.1 amd64 works like a charm 😀

TCWORLD, 2020-07-14:
Hurrah, 5th times the charm :D

marcocipriani01, 2020-07-15:
I confirm that the latest version works flawless on Ubuntu, bug closed! Looking forward to the next stable release :smile:

Closed 2020-07-15.

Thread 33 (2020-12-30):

Changing COM baud rate

CyberianIce, 2020-12-30:
Awesome astrowork!

Actually I have three questions:

1. Is it possible to increase COM baud rate up to 57600, meaning, would that possibly affect avrdude?
2. Is it possible to configure different microstepping configuration for per axis? I.e RA 1/32 and DEC 1/16
3. Is there a way to switch from North to South sidereal tracking direction without reflashing configuration (in driver?)

kaito83, 2021-01-22:
2. You can cheat If you double or half the like motor gear ratios
3. Why do you want to change direction when You can do this from EQMOD

CyberianIce, 2021-01-22:
3. I don't use EQMOD nor ASCOM. I use this with INDI server on Raspberry PI, Joystick and android App (IPARCOS). Recently I discovered that I can connect Arduino MEGA via UART port on RPi and TTL logic level converter (because RPi works with +3.3V). This way I don't need udev, or USB and I can connect multiple AstroEQ devices to single RPi INDI server and I can use INDI via serial pins or ASCOM via USB with double hardware switch. And everything works flawlessly!

kaito83, 2021-01-22:
This is ASCOM independent.
And I also have raspi so:
2. you have to change the in the firmware gear ratio(example): RA 2, DEC 4
3. Find some research just a little help -15,041067

CyberianIce, 2021-01-23:
What about baud rate? Is it safe to increase, what cloud possibly impact?

TCWORLD, 2021-01-23:
Why do you want to increase the baud rate?
Doing so won't make the AstroEQ run any faster. In practice it will likely result in lower reliability as the command processing loop may not be able to keep up, and hence start losing characters.

The firmware for the AstroEQ is already push the limit of what an AVR can do in terms of multi-tasking (controlling two motors, while also interfacing with the PC).

CyberianIce, 2021-01-23:
I need to test that on my own. So far i found 38400 with smaller timer and bigger buffer noticably more responsive. May be due to my setup which include additional modules like I²C display (for encoder values) and HC-05. I believe there are more framing errors on 9800

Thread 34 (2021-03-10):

Usb connection

samuele9581, 2021-03-10:
Hi Tom!
I've finally programmed the atmega and the Pic.
But the USB connection doesn't work at all with my pc.
I tried 2 different cables and the power sources...but nothing...
The USB led is always off but the status and pwr led are on.
I made 2 PCB and both have the same problem...
Do you have any suggestions?

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

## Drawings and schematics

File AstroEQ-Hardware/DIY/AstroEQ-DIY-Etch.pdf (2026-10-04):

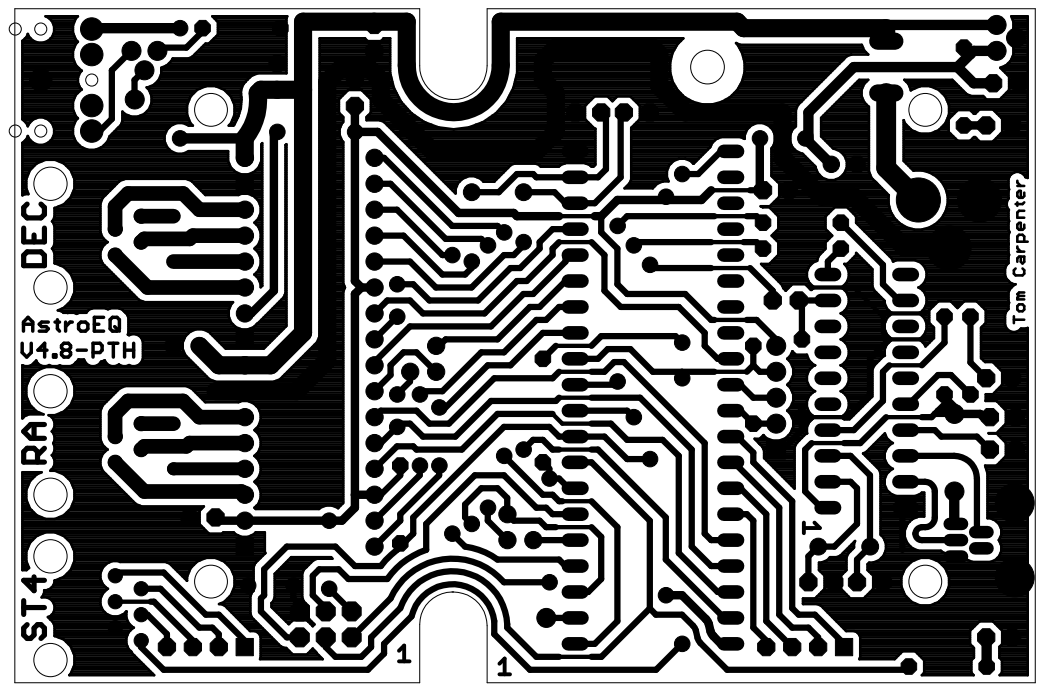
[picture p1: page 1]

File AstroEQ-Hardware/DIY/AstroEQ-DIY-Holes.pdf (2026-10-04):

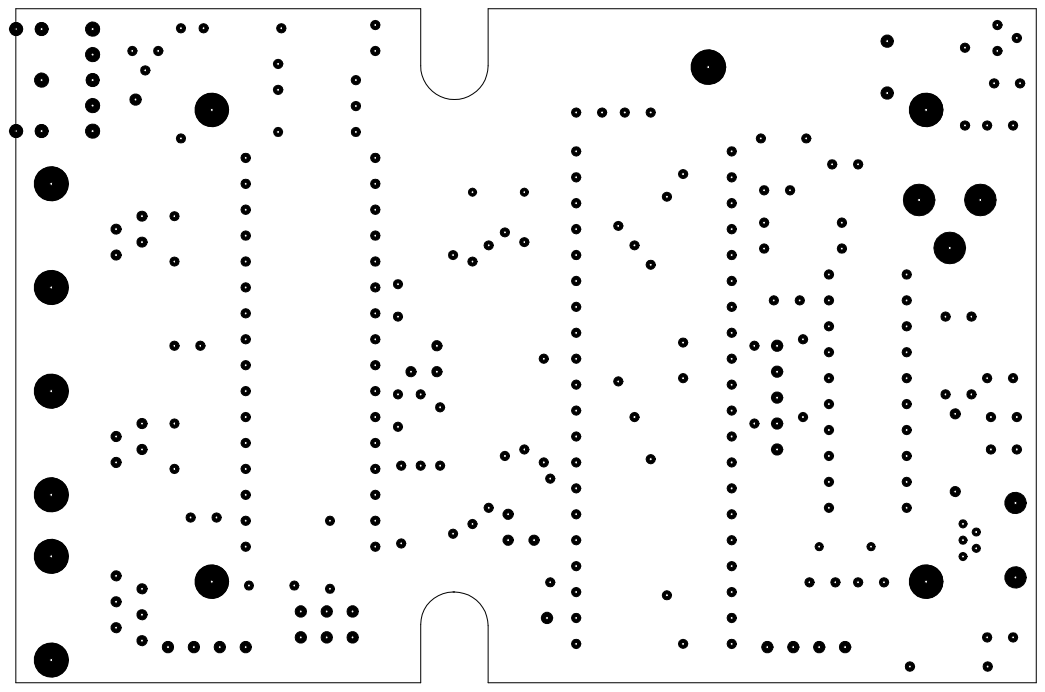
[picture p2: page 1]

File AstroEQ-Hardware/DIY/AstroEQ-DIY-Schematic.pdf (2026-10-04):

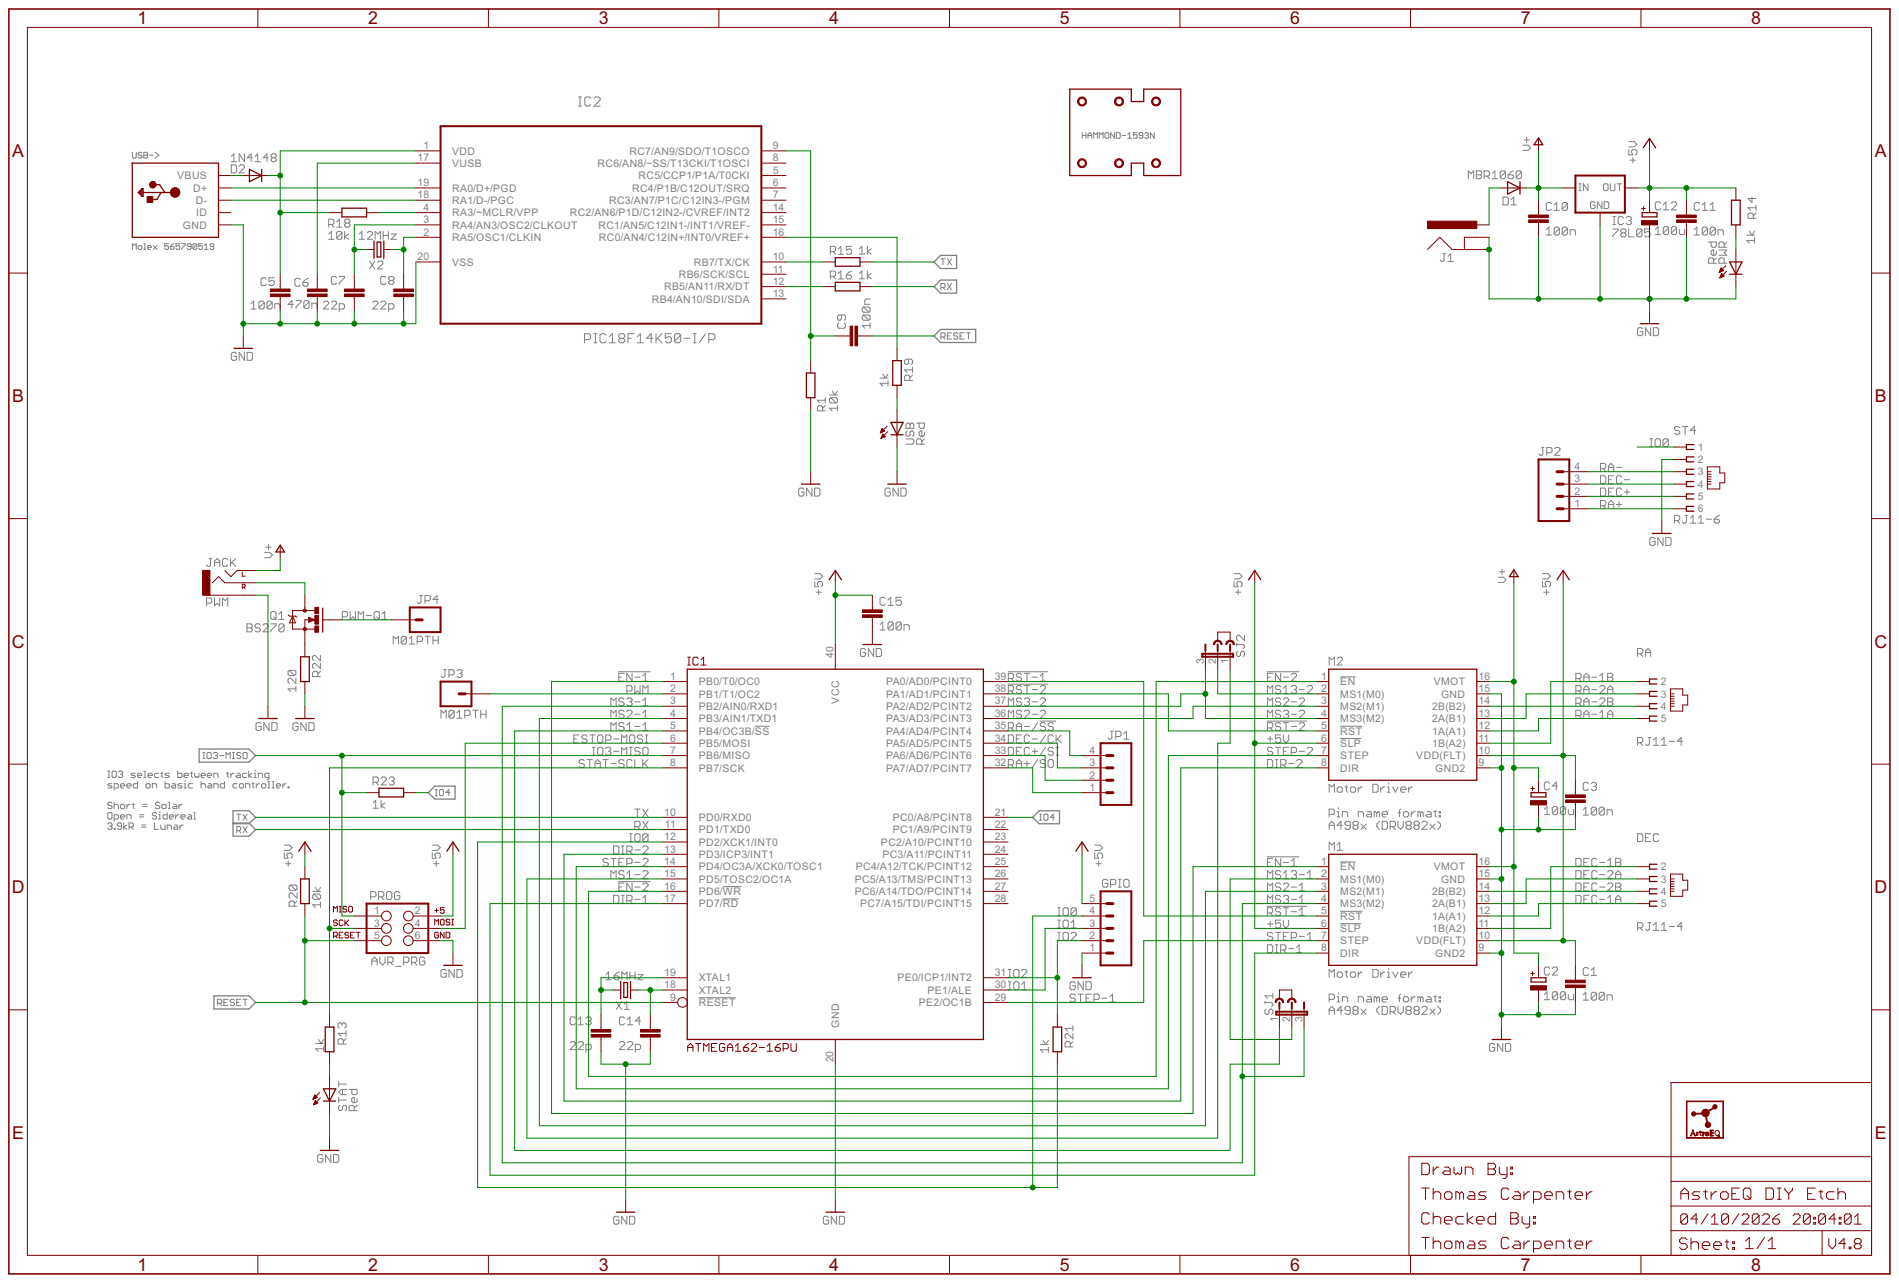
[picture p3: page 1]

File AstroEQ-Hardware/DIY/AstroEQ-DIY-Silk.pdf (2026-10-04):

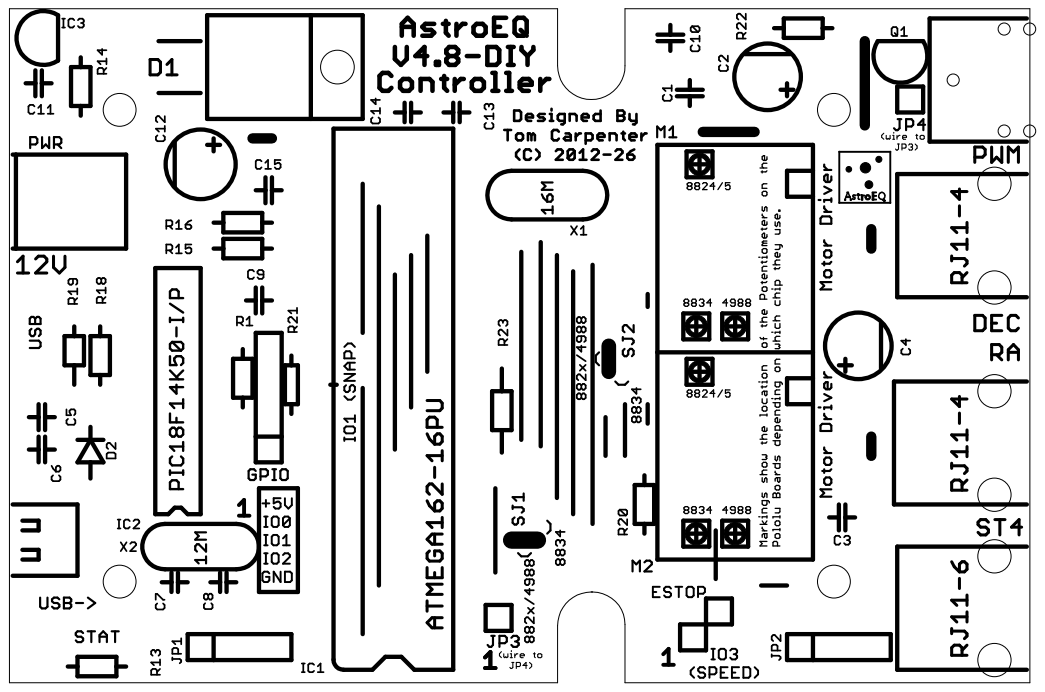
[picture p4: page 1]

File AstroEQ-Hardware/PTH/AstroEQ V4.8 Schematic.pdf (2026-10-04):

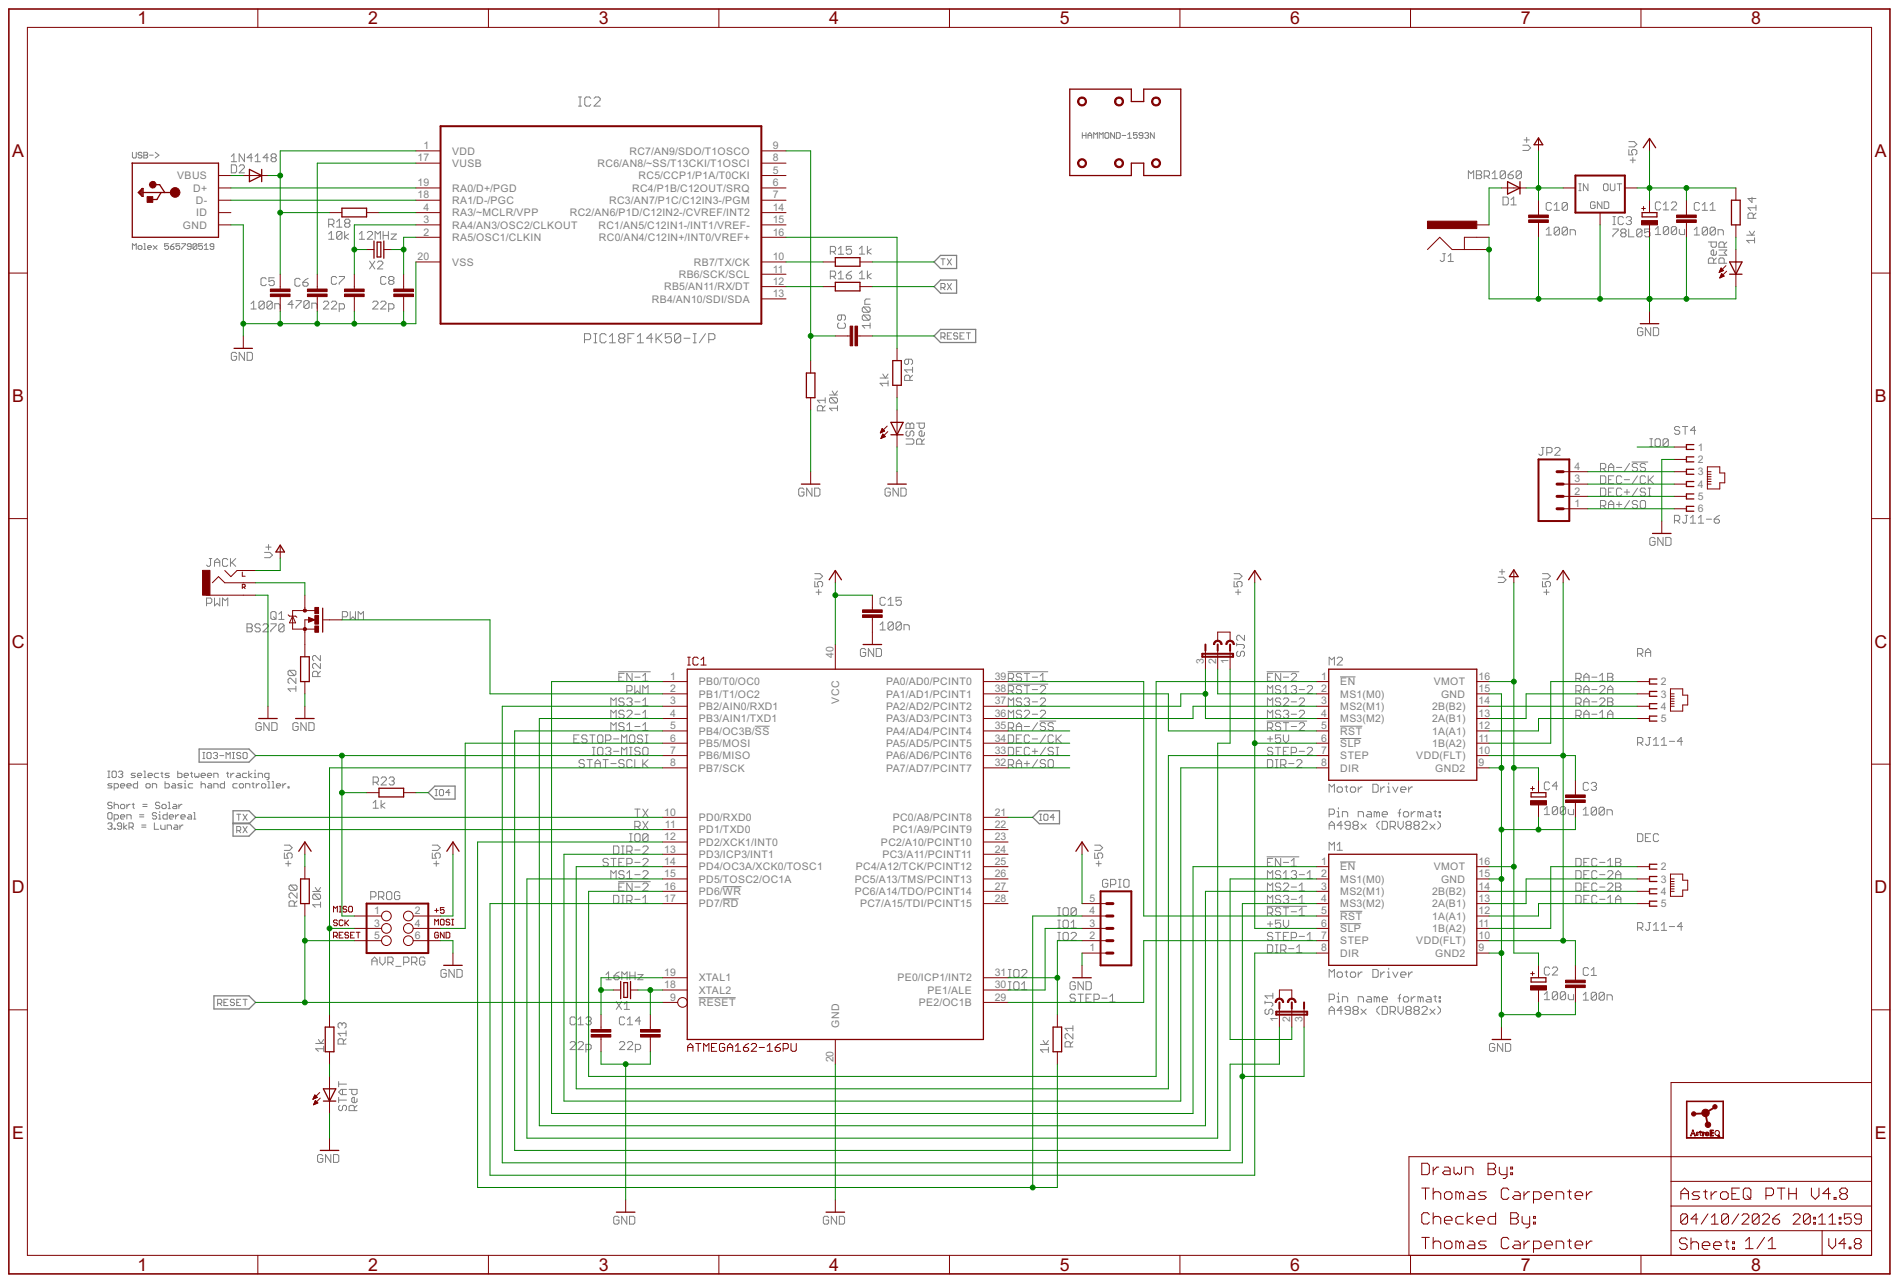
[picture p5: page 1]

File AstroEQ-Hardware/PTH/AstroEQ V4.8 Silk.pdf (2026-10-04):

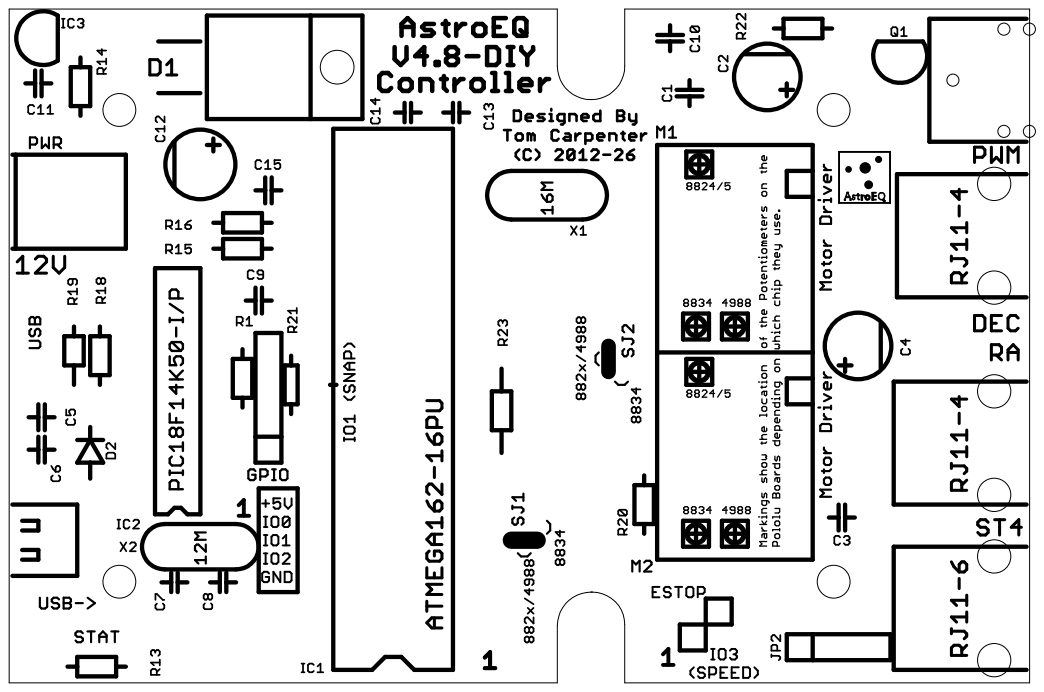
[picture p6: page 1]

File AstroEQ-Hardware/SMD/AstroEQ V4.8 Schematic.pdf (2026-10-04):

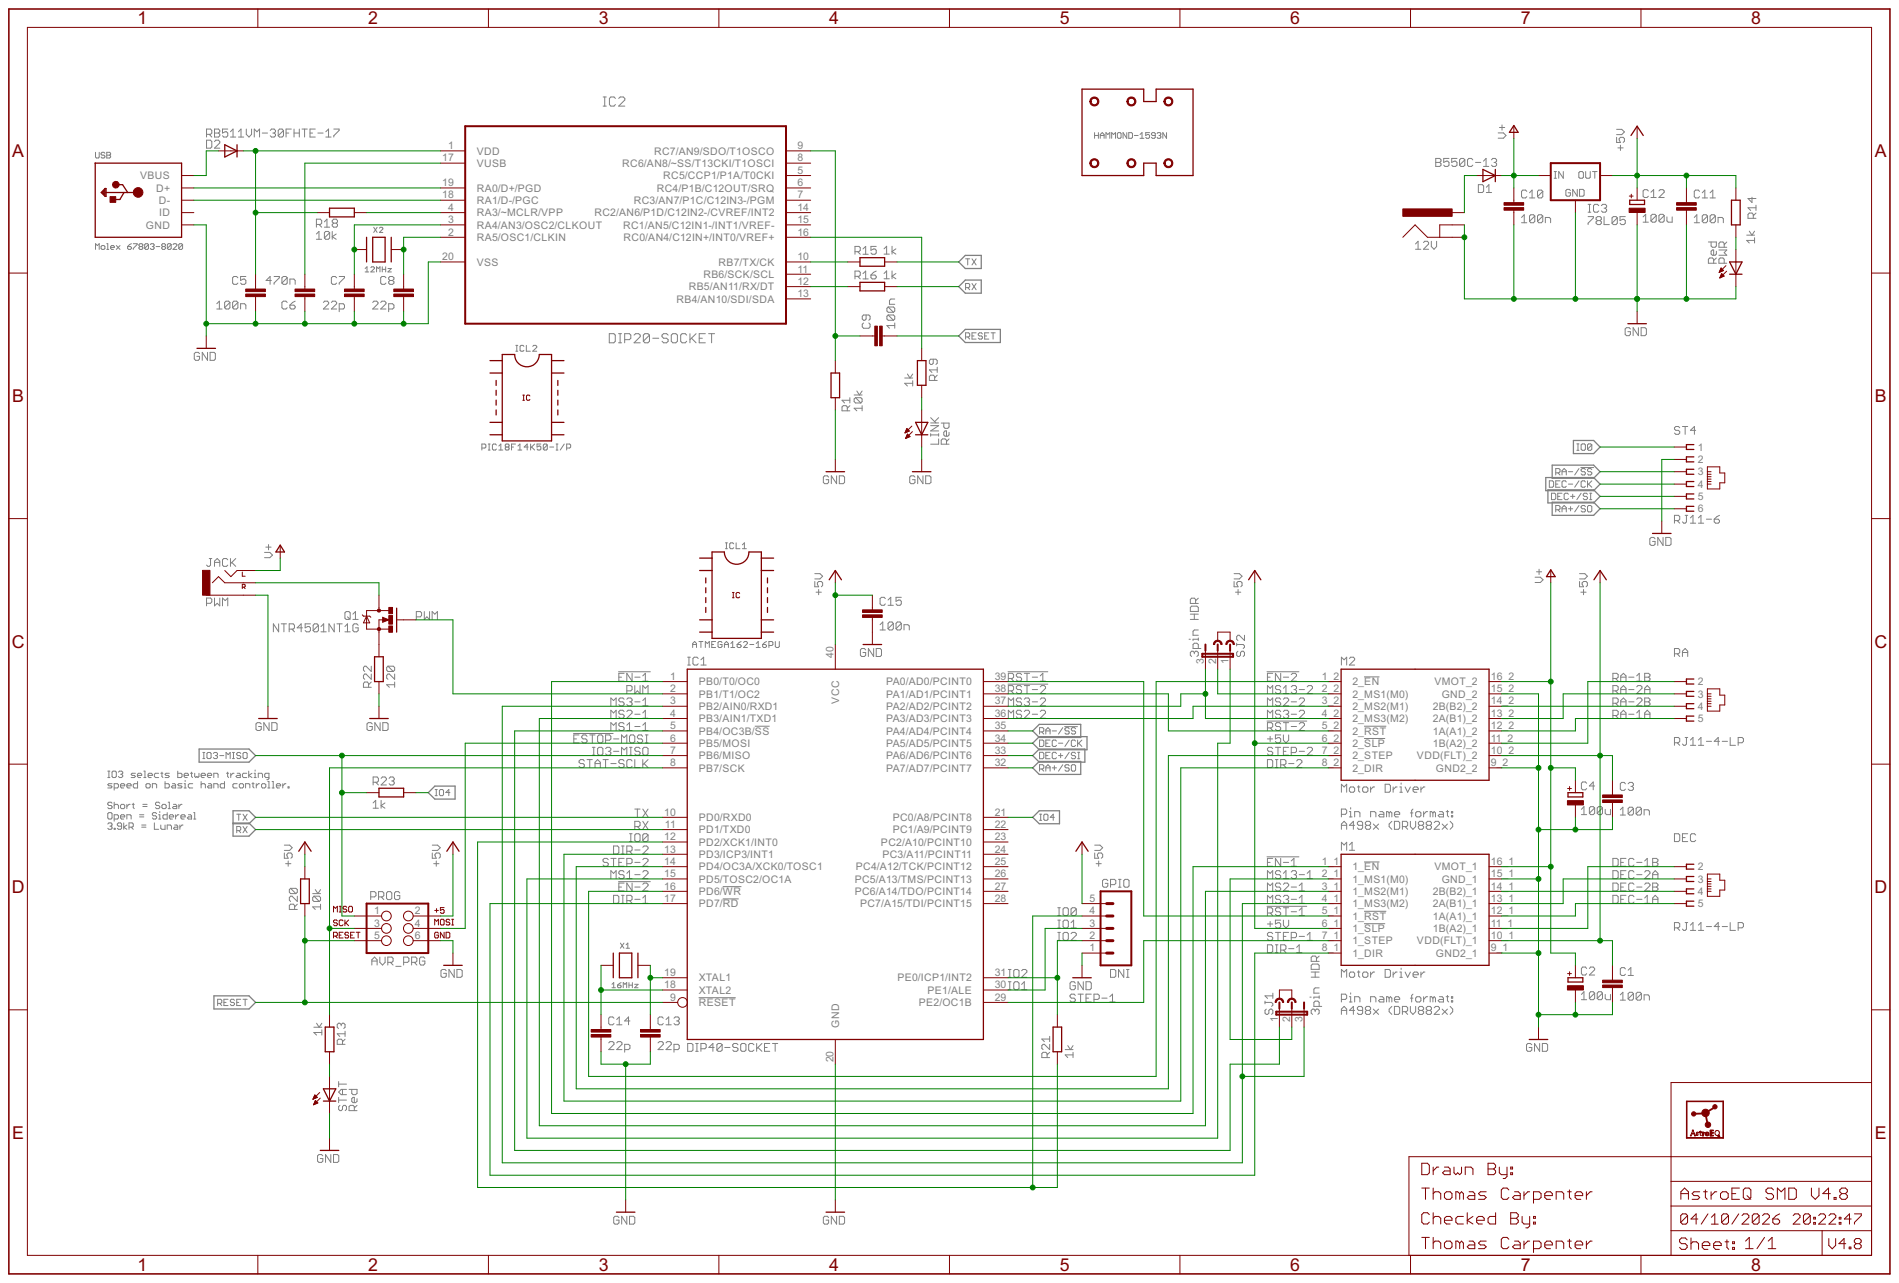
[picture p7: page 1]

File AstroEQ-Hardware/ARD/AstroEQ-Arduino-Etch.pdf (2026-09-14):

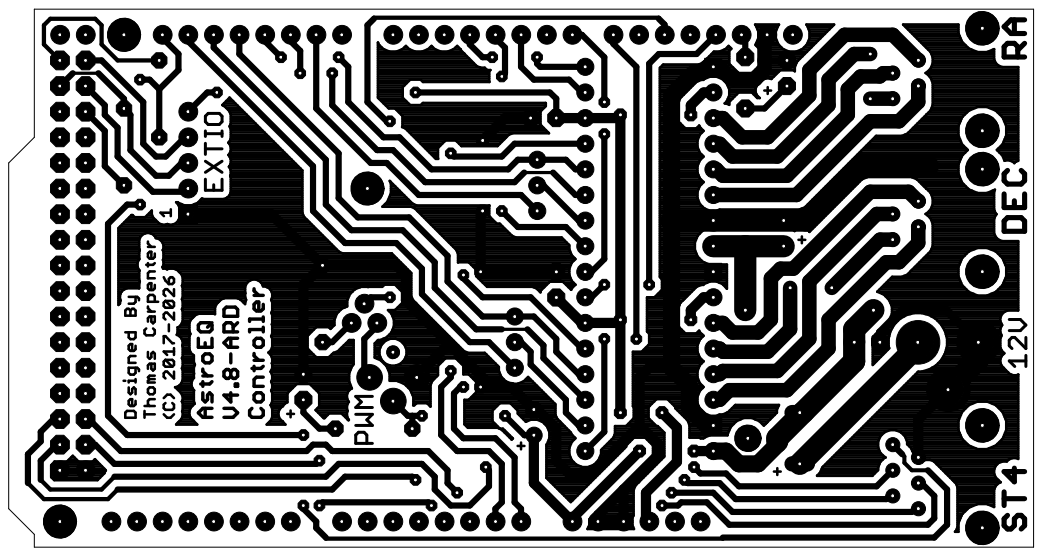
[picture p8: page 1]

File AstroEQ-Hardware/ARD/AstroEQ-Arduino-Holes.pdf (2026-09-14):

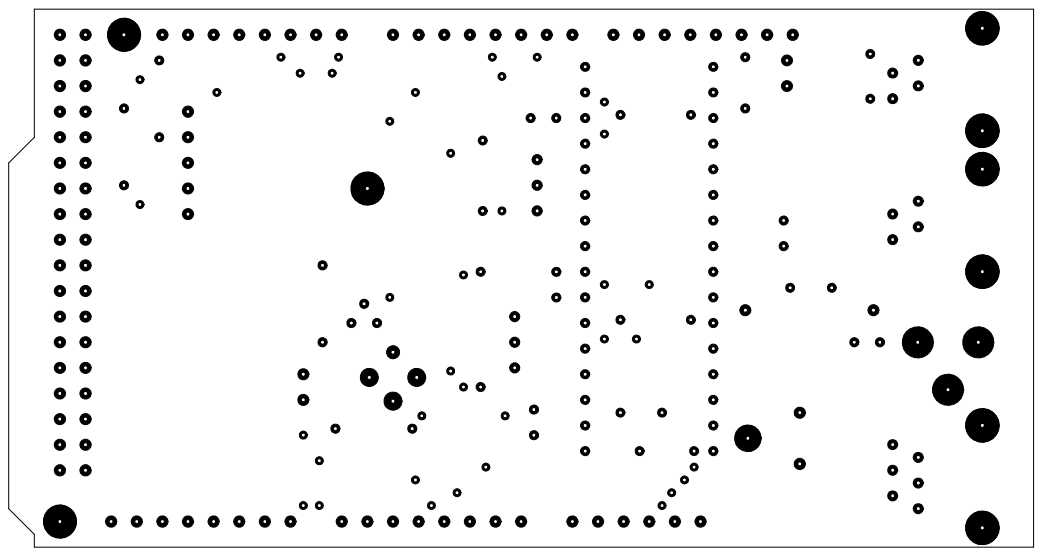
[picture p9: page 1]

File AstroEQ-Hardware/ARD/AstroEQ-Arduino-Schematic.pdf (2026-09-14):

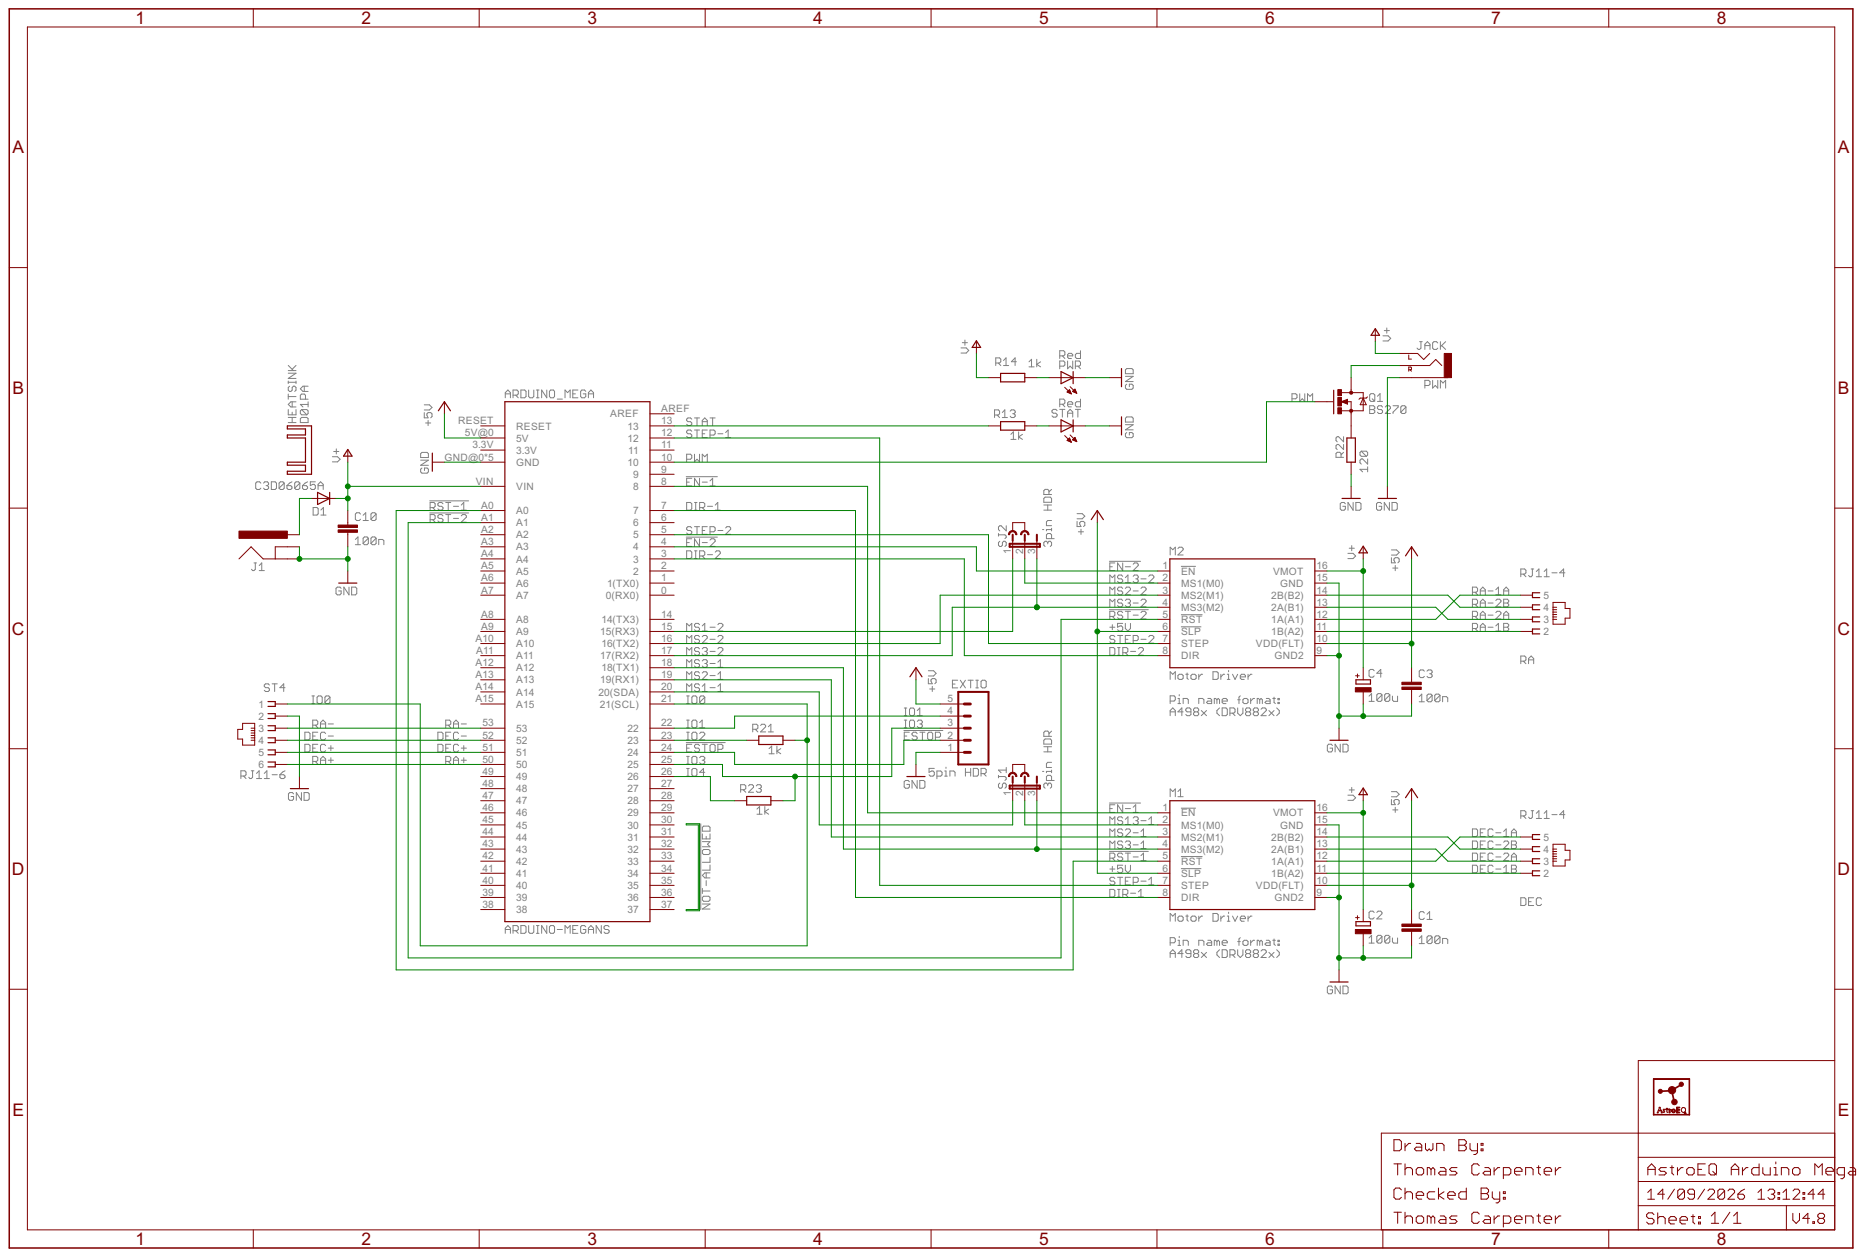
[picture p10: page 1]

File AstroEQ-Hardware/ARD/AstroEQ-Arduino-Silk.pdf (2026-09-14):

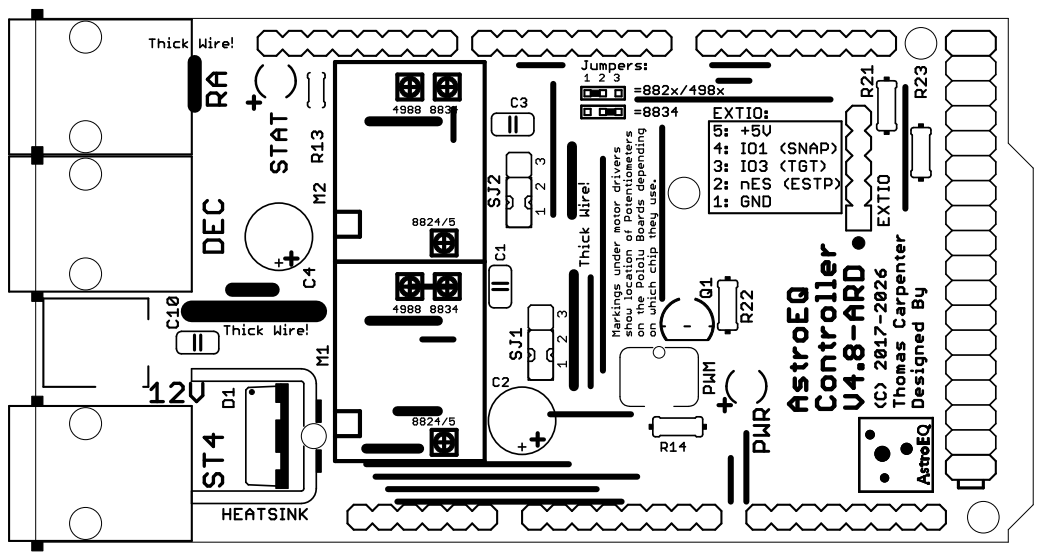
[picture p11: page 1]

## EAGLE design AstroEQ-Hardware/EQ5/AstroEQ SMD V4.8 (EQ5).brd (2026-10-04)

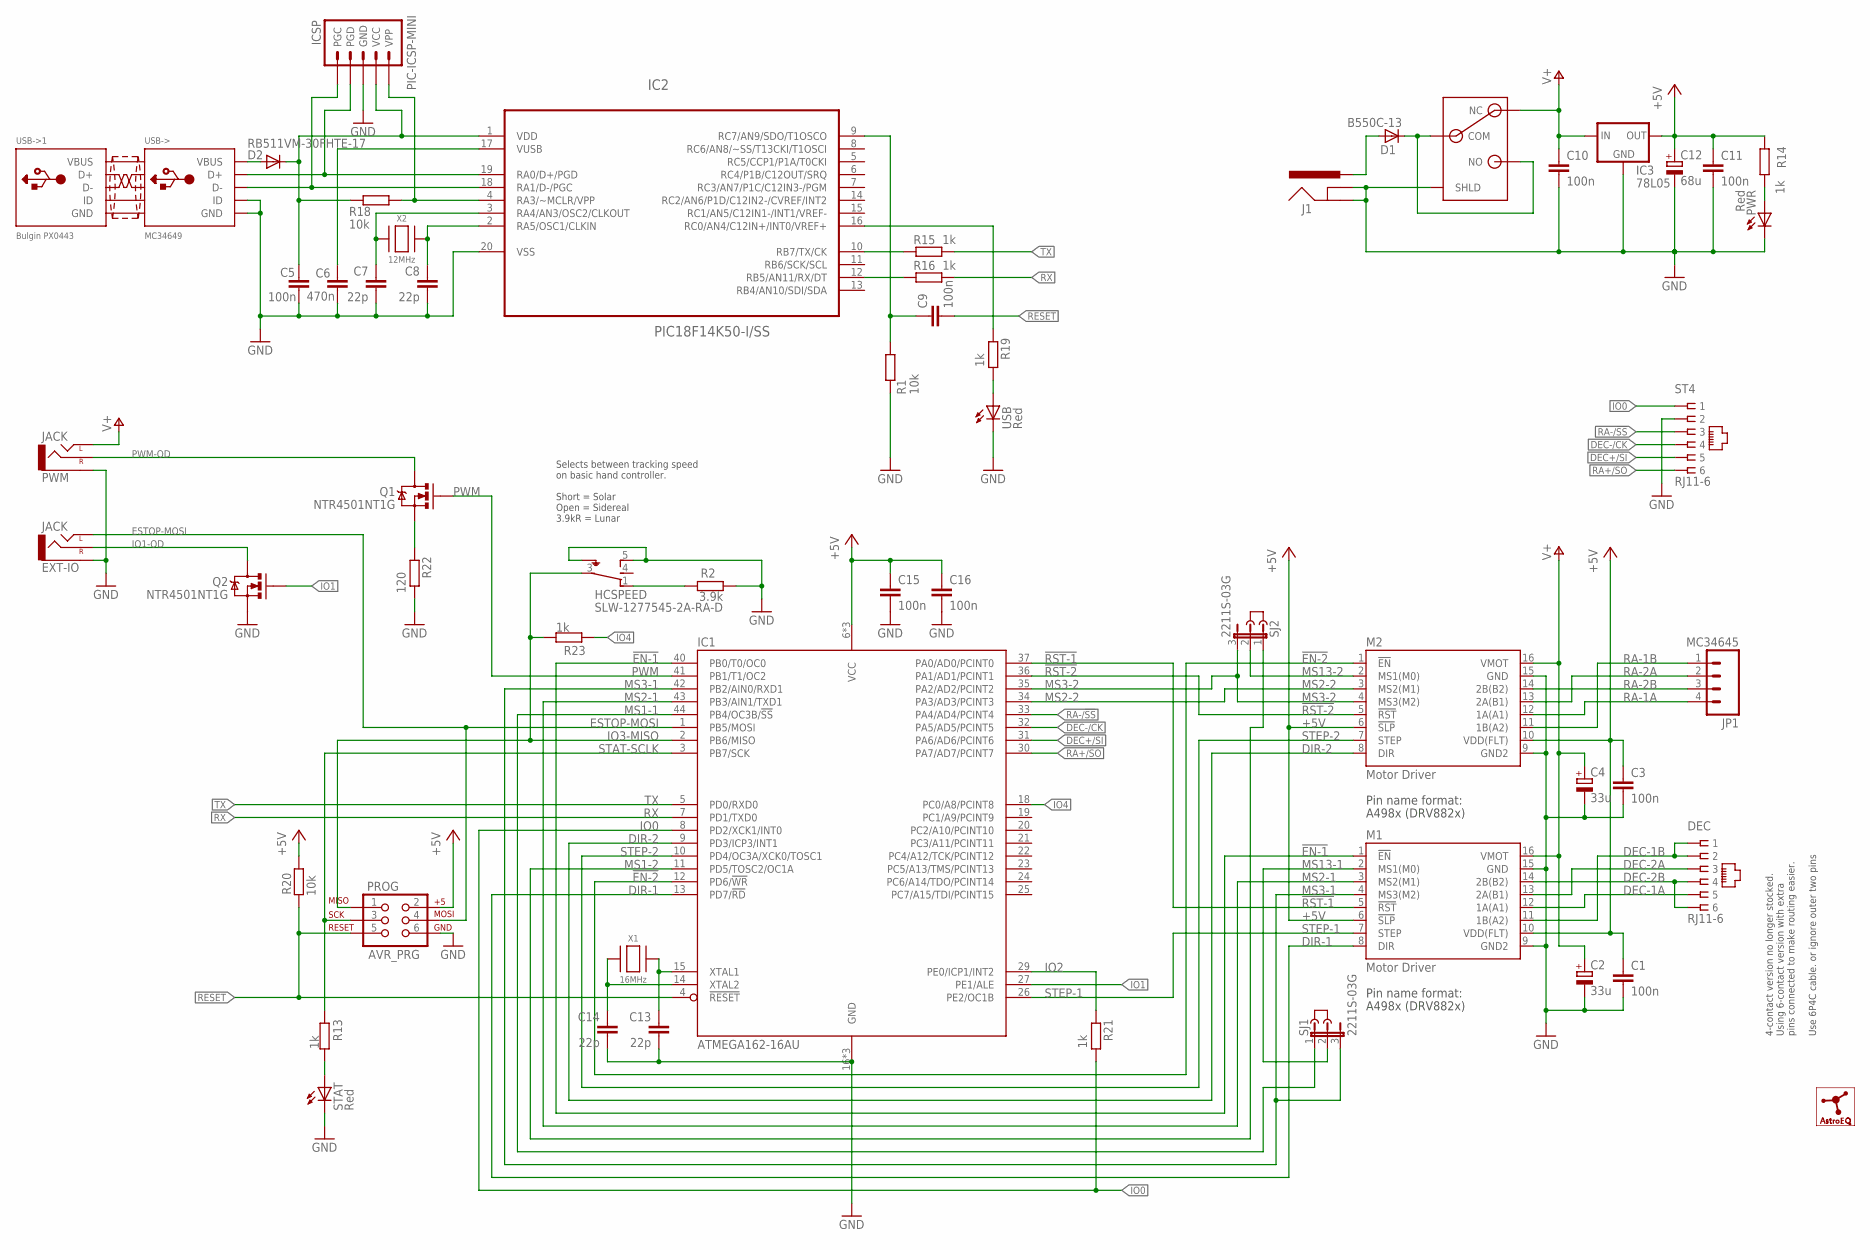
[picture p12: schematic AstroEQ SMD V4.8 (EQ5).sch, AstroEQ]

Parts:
C1, C3, C5, C9, C10, C11, C15, C16: 100n; C0603; MPN MC0603F104Z250CT
C2, C4: 33u; SMC_C; MPN T491C336K025AT
C6: 470n; C0603; MPN MC0603F474Z160CT
C7, C8, C13, C14: 22p; C0603; MPN MC0603N220J500CT
C12: 68u; SMC_C; MPN TPSC686K016R0125
D1: B550C-13; SMC; MPN B550C-13-F
D2: RB511VM-30FHTE-17; SOD-323; MPN RB511VM-30FHTE-17
DEC: RJ11-6; RJ11-NO_SHIELD; MPN 95503-2661
EXT-IO: JACK; AUDIO-JACK-3.5MM-VERT
HCSPEED: SLW-1277545-2A-RA-D; SLW-127
IC1: ATMEGA162-16AU; TQFP44; MPN ATMEGA162-16AU
IC2: PIC18F14K50-I/SS; SS20
IC3: 78L05; SOT23; MPN TS78L05CX RFG
ICSP: PIC-ICSP-MINI
J1: POWER_JACKPANEL; POWER_JACK_PANEL; MPN PCL712AS
J2, J3: DNI; JUMP; MPN 969102-0000-DA
JP1: MC34645; MOLEX-1X4; MPN MC34645
LOGO1: ASTROEQ5MM; ASTROEQ-SMALL
M1, M2: Motor Driver; DIP16-W; MPN CES-116-01-T-S
PROG: AVR_PRG; 2X3; MPN 826632-3
PWM: JACK; AUDIO-JACK-3.5MM-VERT
PWR: Red; LED3MM; MPN L-424HDT
PWR-SW: SWITCH; SPST; MPN AE101J1V3B004
Q1, Q2: NTR4501NT1G; SOT23-3; MPN NTR4501NT1G
R1, R18, R20: 10k; R0603; MPN MCWR06X1002FTL
R2: 3.9k; R0603; MPN MCWR06X1001FTL
R13, R14, R15, R16, R19, R21, R23: 1k; R0603; MPN MCWR06X1001FTL
R22: 120; R0805; MPN MCWR08X1200FTL
SJ1, SJ2: 2211S-03G; JP2; MPN 2211S-03G
ST4: RJ11-6; RJ11-NO_SHIELD; MPN 95503-2661
STAT: Red; LED3MM; MPN L-424HDT
USB: Red; LED3MM; MPN L-424HDT
USB->: MC34649; 22-23-2051; MPN MC34647
X1: 16MHz; NX5032; MPN 7A-16.000MAAJ-T
X2: 12MHz; NX5032; MPN 7A-12.000MAAJ-T

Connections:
!EN-1: IC1.40 (PB0/T0/OC0), M1.1 (!EN)
!EN-2: IC1.12 (PD6/!WR), M2.1 (!EN)
!RST-1: IC1.37 (PA0/AD0/PCINT0), M1.5 (!RST)
!RST-2: IC1.36 (PA1/AD1/PCINT1), M2.5 (!RST)
+5V: C1.1, C3.1, C11.1, C12.+, C15.1, C16.1, IC1.6 (VCC), IC1.17 (VCC), IC1.38 (VCC), IC3.1 (OUT), M1.6 (!SLP), M1.10 (VDD(FLT)), M2.6 (!SLP), M2.10 (VDD(FLT)), PROG.2, R14.1, R20.2
AVROSC1: C13.1, IC1.15 (XTAL1), X1.1
AVROSC2: C14.1, IC1.14 (XTAL2), X1.2
DEC+/SI: IC1.31 (PA6/AD6/PCINT6), ST4.5
DEC-1A: DEC.5, M1.12 (1A(A1))
DEC-1B: DEC.1, DEC.2, M1.11 (1B(A2))
DEC-2A: DEC.3, M1.13 (2A(B1))
DEC-2B: DEC.4, DEC.6, M1.14 (2B(B2))
DEC-/CK: IC1.32 (PA5/AD5/PCINT5), ST4.4
DIR-1: IC1.13 (PD7/!RD), M1.8 (DIR)
DIR-2: IC1.9 (PD3/ICP3/INT1), M2.8 (DIR)
DTR: C9.1, IC2.9 (RC7/AN9/SDO/T1OSCO), R1.1
D_N: IC2.18 (RA1/D-/PGC), ICSP.5 (PGC), USB->.2 (D-)
D_P: IC2.19 (RA0/D+/PGD), ICSP.4 (PGD), USB->.3 (D+)
ESTOP-MOSI: EXT-IO.2 (LEFT), IC1.1 (PB5/MOSI), PROG.4
GND: C1.2, C2.-, C3.2, C4.-, C5.2, C6.1, C7.2, C8.2, C10.2, C11.2, C12.-, C13.2, C14.2, C15.2, C16.2, EXT-IO.1 (SLEEVE), HCSPEED.5 (O), HCSPEED.S1 (SH), HCSPEED.S2 (SH), IC1.16 (GND), IC1.28 (GND), IC1.39 (GND), IC2.20 (VSS), IC3.3 (GND), ICSP.3 (GND), J1.SHUNT (GNDBREAK), J1.SLEEVE (GND), M1.9 (GND2), M1.15 (GND), M2.9 (GND2), M2.15 (GND), PROG.6, PWM.1 (SLEEVE), PWR.K (C), PWR-SW.S1 (SHLD), PWR-SW.S2 (SHLD), PWR-SW.S3 (SHLD), PWR-SW.S4 (SHLD), Q2.2 (S), R1.2, R2.2, R22.1, ST4.2, STAT.K (C), USB.K (C), USB->.4 (GND), USB->.5 (ID)
IO0: IC1.8 (PD2/XCK1/INT0), R21.1, ST4.1
IO1: IC1.27 (PE1/ALE), Q2.1 (G)
IO1-OD: EXT-IO.3 (RIGHT), Q2.3 (D)
IO2: IC1.29 (PE0/ICP1/INT2), R21.2
IO3-MISO: HCSPEED.3, IC1.2 (PB6/MISO), PROG.1, R23.2
IO4: IC1.18 (PC0/A8/PCINT8), R23.1
MCLR: IC2.4 (RA3/~MCLR/VPP), ICSP.1 (VPP), R18.1
MS1-1: IC1.44 (PB4/OC3B/!SS), SJ1.1
MS1-2: IC1.11 (PD5/TOSC2/OC1A), SJ2.1
MS2-1: IC1.43 (PB3/AIN1/TXD1), M1.3 (MS2(M1))
MS2-2: IC1.34 (PA3/AD3/PCINT3), M2.3 (MS2(M1))
MS3-1: IC1.42 (PB2/AIN0/RXD1), M1.4 (MS3(M2)), SJ1.3
MS3-2: IC1.35 (PA2/AD2/PCINT2), M2.4 (MS3(M2)), SJ2.3
MS13-1: M1.2 (MS1(M0)), SJ1.2
MS13-2: M2.2 (MS1(M0)), SJ2.2
unnamed: HCSPEED.1 (S), R2.1
PWM: IC1.41 (PB1/T1/OC2), Q1.1 (G)
PWM-OD: PWM.3 (RIGHT), Q1.3 (D)
PWM-RES: Q1.2 (S), R22.2
PWRLED: PWR.A, R14.2
RA+/SO: IC1.30 (PA7/AD7/PCINT7), ST4.6
RA-1A: JP1.4, M2.12 (1A(A1))
RA-1B: JP1.1, M2.11 (1B(A2))
RA-2A: JP1.2, M2.13 (2A(B1))
RA-2B: JP1.3, M2.14 (2B(B2))
RA-/!SS: IC1.33 (PA4/AD4/PCINT4), ST4.3
RESET: C9.2, IC1.4 (!RESET), PROG.5, R20.1
RX: IC1.7 (PD1/TXD0), R16.1
RX(USB): IC2.12 (RB5/AN11/RX/DT), R16.2
STAT-SCLK: IC1.3 (PB7/SCK), PROG.3, R13.1
STATLED: R13.2, STAT.A
STEP-1: IC1.26 (PE2/OC1B), M1.7 (STEP)
STEP-2: IC1.10 (PD4/OC3A/XCK0/TOSC1), M2.7 (STEP)
SWITCH: D1.C, PWR-SW.COM, PWR-SW.NO
TX: IC1.5 (PD0/RXD0), R15.1
TX(USB): IC2.10 (RB7/TX/CK), R15.2
USBLED: R19.1, USB.A
USBOSC1: C8.1, IC2.2 (RA5/OSC1/CLKIN), X2.2
USBOSC2: C7.1, IC2.3 (RA4/AN3/OSC2/CLKOUT), X2.1
USBSTAT: IC2.16 (RC0/AN4/C12IN+/INT0/VREF+), R19.2
V+: C2.+, C4.+, C10.1, IC3.2 (IN), M1.16 (VMOT), M2.16 (VMOT), PWM.2 (LEFT), PWR-SW.NC
VBUS: D2.2 (A), USB->.1 (VBUS)
VIN: D1.A, J1.CENTRE (PWR)
VPIC: C5.1, D2.1 (C), IC2.1 (VDD), ICSP.2 (VCC), R18.2
VUSB: C6.2, IC2.17 (VUSB)

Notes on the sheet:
4-contact version no longer stocked. Using 6-contact version with extra pins connected to make routing easier. Use 6P4C cable. or ignore outer two pins
Selects between tracking speed on basic hand controller. Short = Solar Open = Sidereal 3.9kR = Lunar

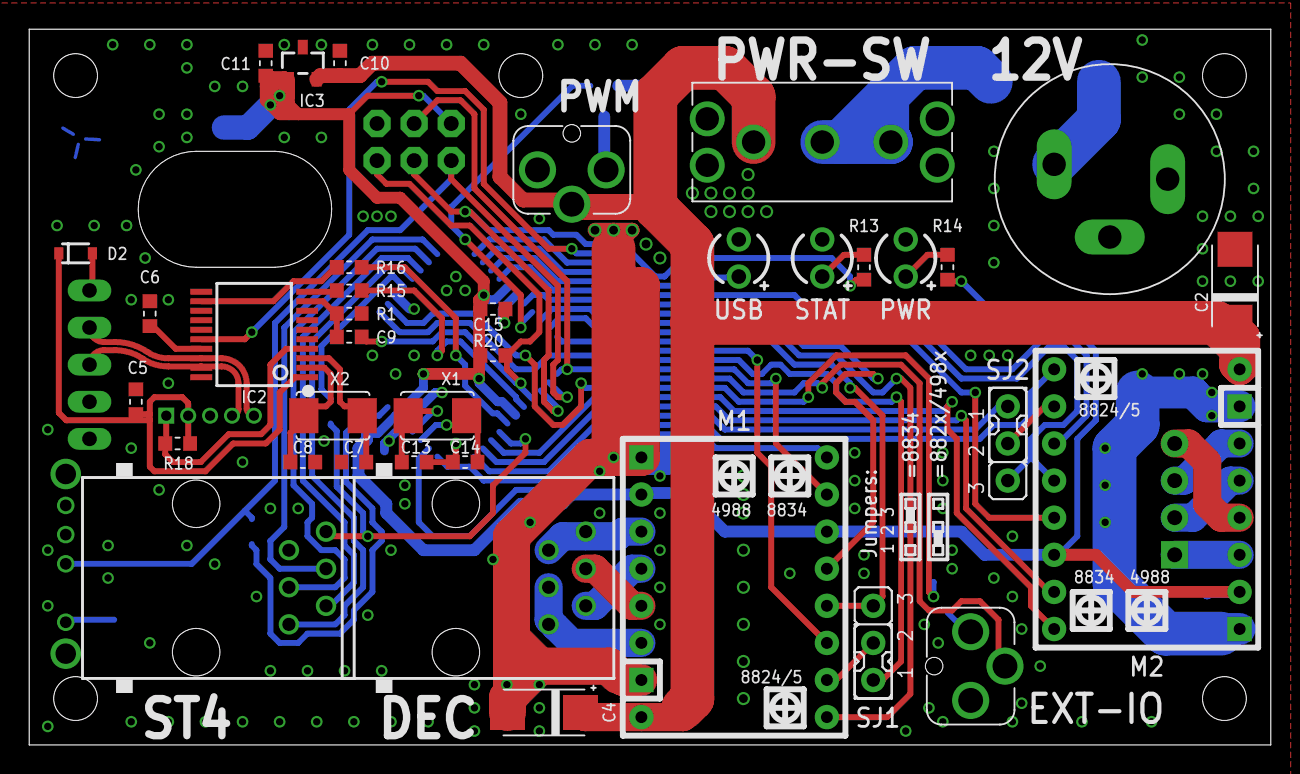
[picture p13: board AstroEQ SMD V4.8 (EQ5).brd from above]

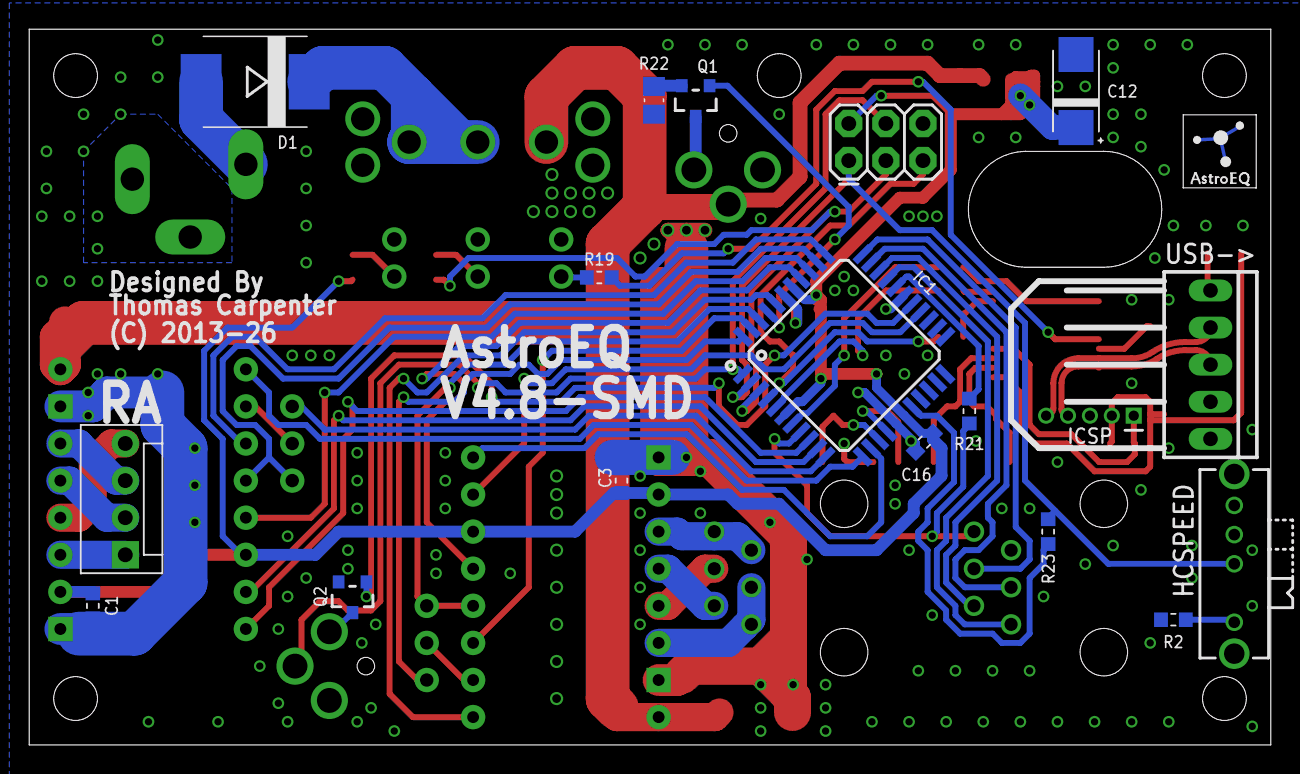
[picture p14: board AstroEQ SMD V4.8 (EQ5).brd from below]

Board: 2 copper layers, 85.0 x 49.0 mm, 58 parts (19 on the bottom side), 65 nets.

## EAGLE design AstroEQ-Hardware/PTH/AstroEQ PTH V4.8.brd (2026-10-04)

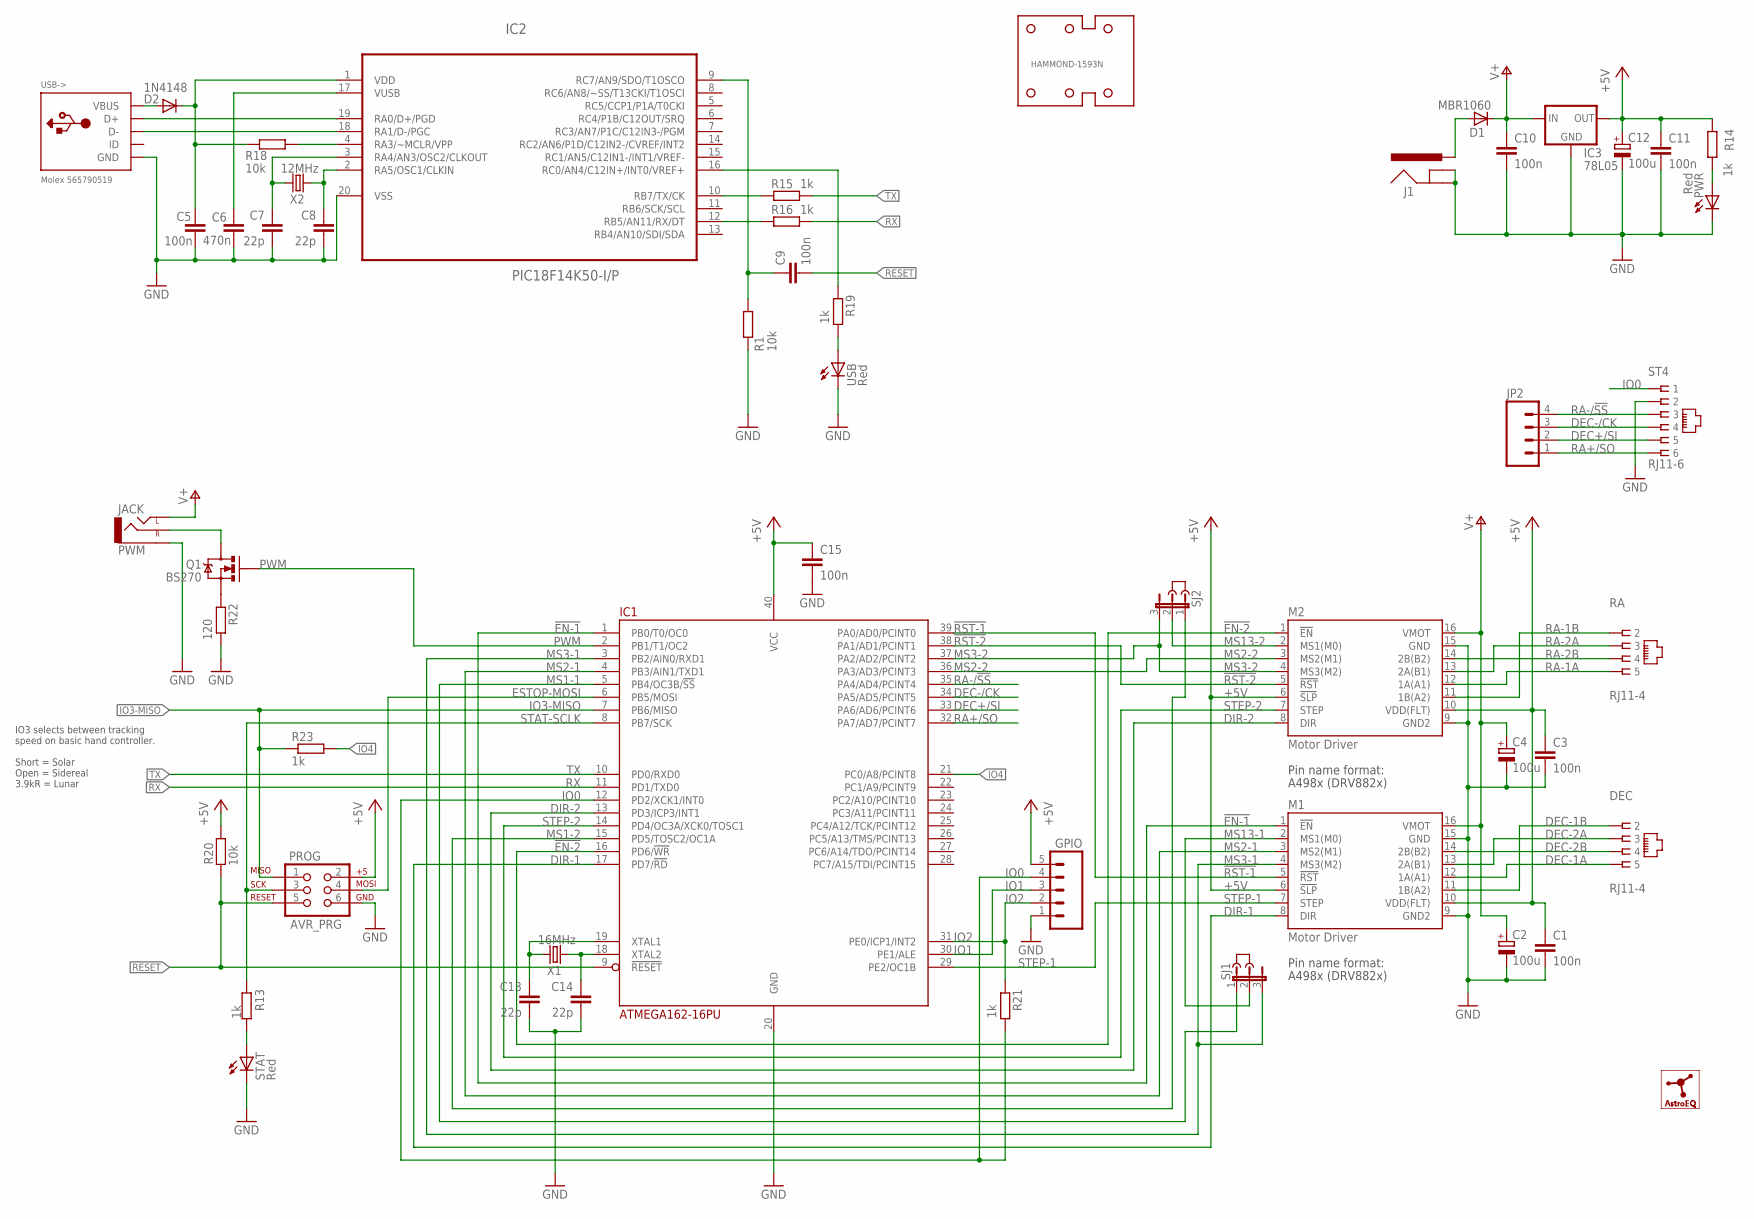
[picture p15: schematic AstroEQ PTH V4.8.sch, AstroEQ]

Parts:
C1, C3, C5, C9, C10, C11, C15: 100n; C025-024X044; MPN SR205C104KAR
C2, C4, C12: 100u; E2,5-7; MPN MCGPR25V107M6.3X11
C6: 470n; C025-024X044; MPN C320C474M5U5TA
C7, C8, C13, C14: 22p; C025-024X044; MPN SR151A220JAR
D1: MBR1060; C221B1A; MPN MBR1060
D2: 1N4148; DIODE-1N4148; MPN 1N4148.
DEC: RJ11-4; RJ11-NO_SHIELD-4; MPN 95501-2641
GPIO: M05PTH; 1X05; MPN SSF211X050
HAMMOND-1593N: HAMMOND-1593N-4HOLE; HAMMOND-1593N4HOLES; MPN 1593NBK
IC1: ATMEGA162-16PU; DIL40; MPN ATMEGA162-16PU
IC2: PIC18F14K50-I/P; DIL20
IC3: 78L05; TO-92; MPN LM78L05ACZX
J1: POWER_JACKPTH; POWER_JACK_PTH; MPN MJ-179PH
J2, J3: JUMPER; JUMP
JP2: M04PTH; 1X04
LOGO1: ASTROEQ5MM; ASTROEQ-SMALL
M1, M2: Motor Driver; DIP16-W; MPN CES-116-01-T-S
PROG: AVR_PRG; 2X3; MPN 826632-3
PWM: JACK; AUDIO-JACK; MPN FC68131
PWR: Red; LED3MM; MPN L-424HDT
Q1: BS270; TO-92; MPN BS270
R1, R18, R20: 10k; 0204/7; MPN MF12 10K
R13, R14, R15, R16, R19, R21: 1k; 0204/7; MPN MF12 1K
R22: 120; 0204/7; MPN MF12 120R
R23: 1k; 0207/10; MPN MF12 1K
RA: RJ11-4; RJ11-NO_SHIELD-4; MPN 95501-2641
SJ1, SJ2: JP2EL; JP2L
ST4: RJ11-6; RJ11-NO_SHIELD; MPN 95501-2661
STAT: Red; LED3MM; MPN L-424HDT
USB: Red; LED3MM; MPN L-424HDT
USB->: Molex 565790519; USB-MINIB-THM-MOLEX; MPN 565790519
X1: 16MHz; HC49US; MPN 9B-16.000MEEJ-B
X2: 12MHz; HC49US; MPN 9B-12.000MAAJ-B

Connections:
!EN-1: IC1.1 (PB0/T0/OC0), M1.1 (!EN)
!EN-2: IC1.16 (PD6/!WR), M2.1 (!EN)
!RST-1: IC1.39 (PA0/AD0/PCINT0), M1.5 (!RST)
!RST-2: IC1.38 (PA1/AD1/PCINT1), M2.5 (!RST)
+5V: C1.1, C3.1, C11.1, C12.+, C15.1, GPIO.5, IC1.40 (VCC), IC3.1 (OUT), M1.6 (!SLP), M1.10 (VDD(FLT)), M2.6 (!SLP), M2.10 (VDD(FLT)), PROG.2, R14.1, R20.2
AVROSC1: C13.1, IC1.19 (XTAL1), X1.2
AVROSC2: C14.1, IC1.18 (XTAL2), X1.1
D+: IC2.19 (RA0/D+/PGD), USB->.D+
D-: IC2.18 (RA1/D-/PGC), USB->.D-
DEC+/SI: IC1.33 (PA6/AD6/PCINT6), JP2.2, ST4.5
DEC-1A: DEC.5, M1.12 (1A(A1))
DEC-1B: DEC.2, M1.11 (1B(A2))
DEC-2A: DEC.3, M1.13 (2A(B1))
DEC-2B: DEC.4, M1.14 (2B(B2))
DEC-/CK: IC1.34 (PA5/AD5/PCINT5), JP2.3, ST4.4
DIR-1: IC1.17 (PD7/!RD), M1.8 (DIR)
DIR-2: IC1.13 (PD3/ICP3/INT1), M2.8 (DIR)
DTR: C9.1, IC2.9 (RC7/AN9/SDO/T1OSCO), R1.1
ESTOP-MOSI: IC1.6 (PB5/MOSI), PROG.4
GND: C1.2, C2.-, C3.2, C4.-, C5.2, C6.1, C7.2, C8.2, C10.2, C11.2, C12.-, C13.2, C14.2, C15.2, GPIO.1, IC1.20 (GND), IC2.20 (VSS), IC3.2 (GND), J1.GND, J1.GNDBREAK, M1.9 (GND2), M1.15 (GND), M2.9 (GND2), M2.15 (GND), PROG.6, PWM.SLEEVE, PWR.K (C), R1.2, R22.1, ST4.2, STAT.K (C), USB.K (C), USB->.GND, USB->.GND1 (GND), USB->.GND4 (GND)
IO0: GPIO.4, IC1.12 (PD2/XCK1/INT0), R21.1, ST4.1
IO1: GPIO.3, IC1.30 (PE1/ALE)
IO2: GPIO.2, IC1.31 (PE0/ICP1/INT2), R21.2
IO3-MISO: IC1.7 (PB6/MISO), PROG.1, R23.1
IO4: IC1.21 (PC0/A8/PCINT8), R23.2
MCLR: IC2.4 (RA3/~MCLR/VPP), R18.1
MS1-1: IC1.5 (PB4/OC3B/!SS), SJ1.1
MS1-2: IC1.15 (PD5/TOSC2/OC1A), SJ2.1
MS2-1: IC1.4 (PB3/AIN1/TXD1), M1.3 (MS2(M1))
MS2-2: IC1.36 (PA3/AD3/PCINT3), M2.3 (MS2(M1))
MS3-1: IC1.3 (PB2/AIN0/RXD1), M1.4 (MS3(M2)), SJ1.3
MS3-2: IC1.37 (PA2/AD2/PCINT2), M2.4 (MS3(M2)), SJ2.3
MS13-1: M1.2 (MS1(M0)), SJ1.2
MS13-2: M2.2 (MS1(M0)), SJ2.2
PWM: IC1.2 (PB1/T1/OC2), Q1.2 (G)
PWM-ILIM: Q1.3 (S), R22.2
PWM-OUT: PWM.RING (RIGHT), Q1.1 (D)
PWRLED: PWR.A, R14.2
RA+/SO: IC1.32 (PA7/AD7/PCINT7), JP2.1, ST4.6
RA-1A: M2.12 (1A(A1)), RA.5
RA-1B: M2.11 (1B(A2)), RA.2
RA-2A: M2.13 (2A(B1)), RA.3
RA-2B: M2.14 (2B(B2)), RA.4
RA-/!SS: IC1.35 (PA4/AD4/PCINT4), JP2.4, ST4.3
RESET: C9.2, IC1.9 (!RESET), PROG.5, R20.1
RX: IC1.11 (PD1/TXD0), R16.1
RX(USB): IC2.12 (RB5/AN11/RX/DT), R16.2
STAT-SCLK: IC1.8 (PB7/SCK), PROG.3, R13.1
STATLED: R13.2, STAT.A
STEP-1: IC1.29 (PE2/OC1B), M1.7 (STEP)
STEP-2: IC1.14 (PD4/OC3A/XCK0/TOSC1), M2.7 (STEP)
TX: IC1.10 (PD0/RXD0), R15.1
TX(USB): IC2.10 (RB7/TX/CK), R15.2
USBLED: R19.1, USB.A
USBOSC1: C8.1, IC2.2 (RA5/OSC1/CLKIN), X2.1
USBOSC2: C7.1, IC2.3 (RA4/AN3/OSC2/CLKOUT), X2.2
USBSTAT: IC2.16 (RC0/AN4/C12IN+/INT0/VREF+), R19.2
V+: C2.+, C4.+, C10.1, D1.C, IC3.3 (IN), M1.16 (VMOT), M2.16 (VMOT), PWM.TIP (LEFT)
VBUS: D2.A, USB->.VBUS
VIN: D1.A, J1.PWR
VPIC: C5.1, D2.C, IC2.1 (VDD), R18.2
VUSB: C6.2, IC2.17 (VUSB)

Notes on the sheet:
IO3 selects between tracking speed on basic hand controller. Short = Solar Open = Sidereal 3.9kR = Lunar

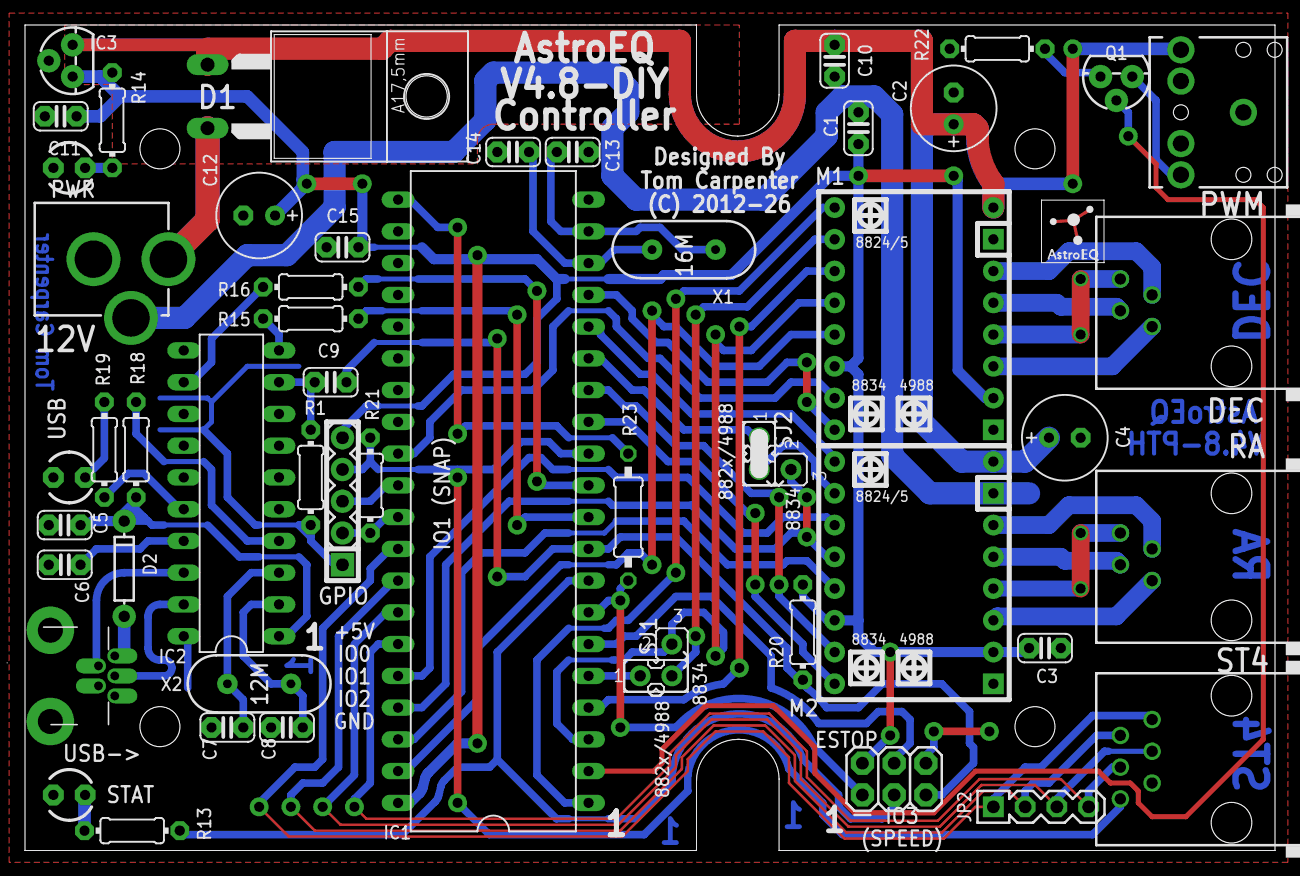
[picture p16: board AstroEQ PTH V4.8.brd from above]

Board: 2 copper layers, 100.0 x 66.0 mm, 54 parts (0 on the bottom side), 62 nets.

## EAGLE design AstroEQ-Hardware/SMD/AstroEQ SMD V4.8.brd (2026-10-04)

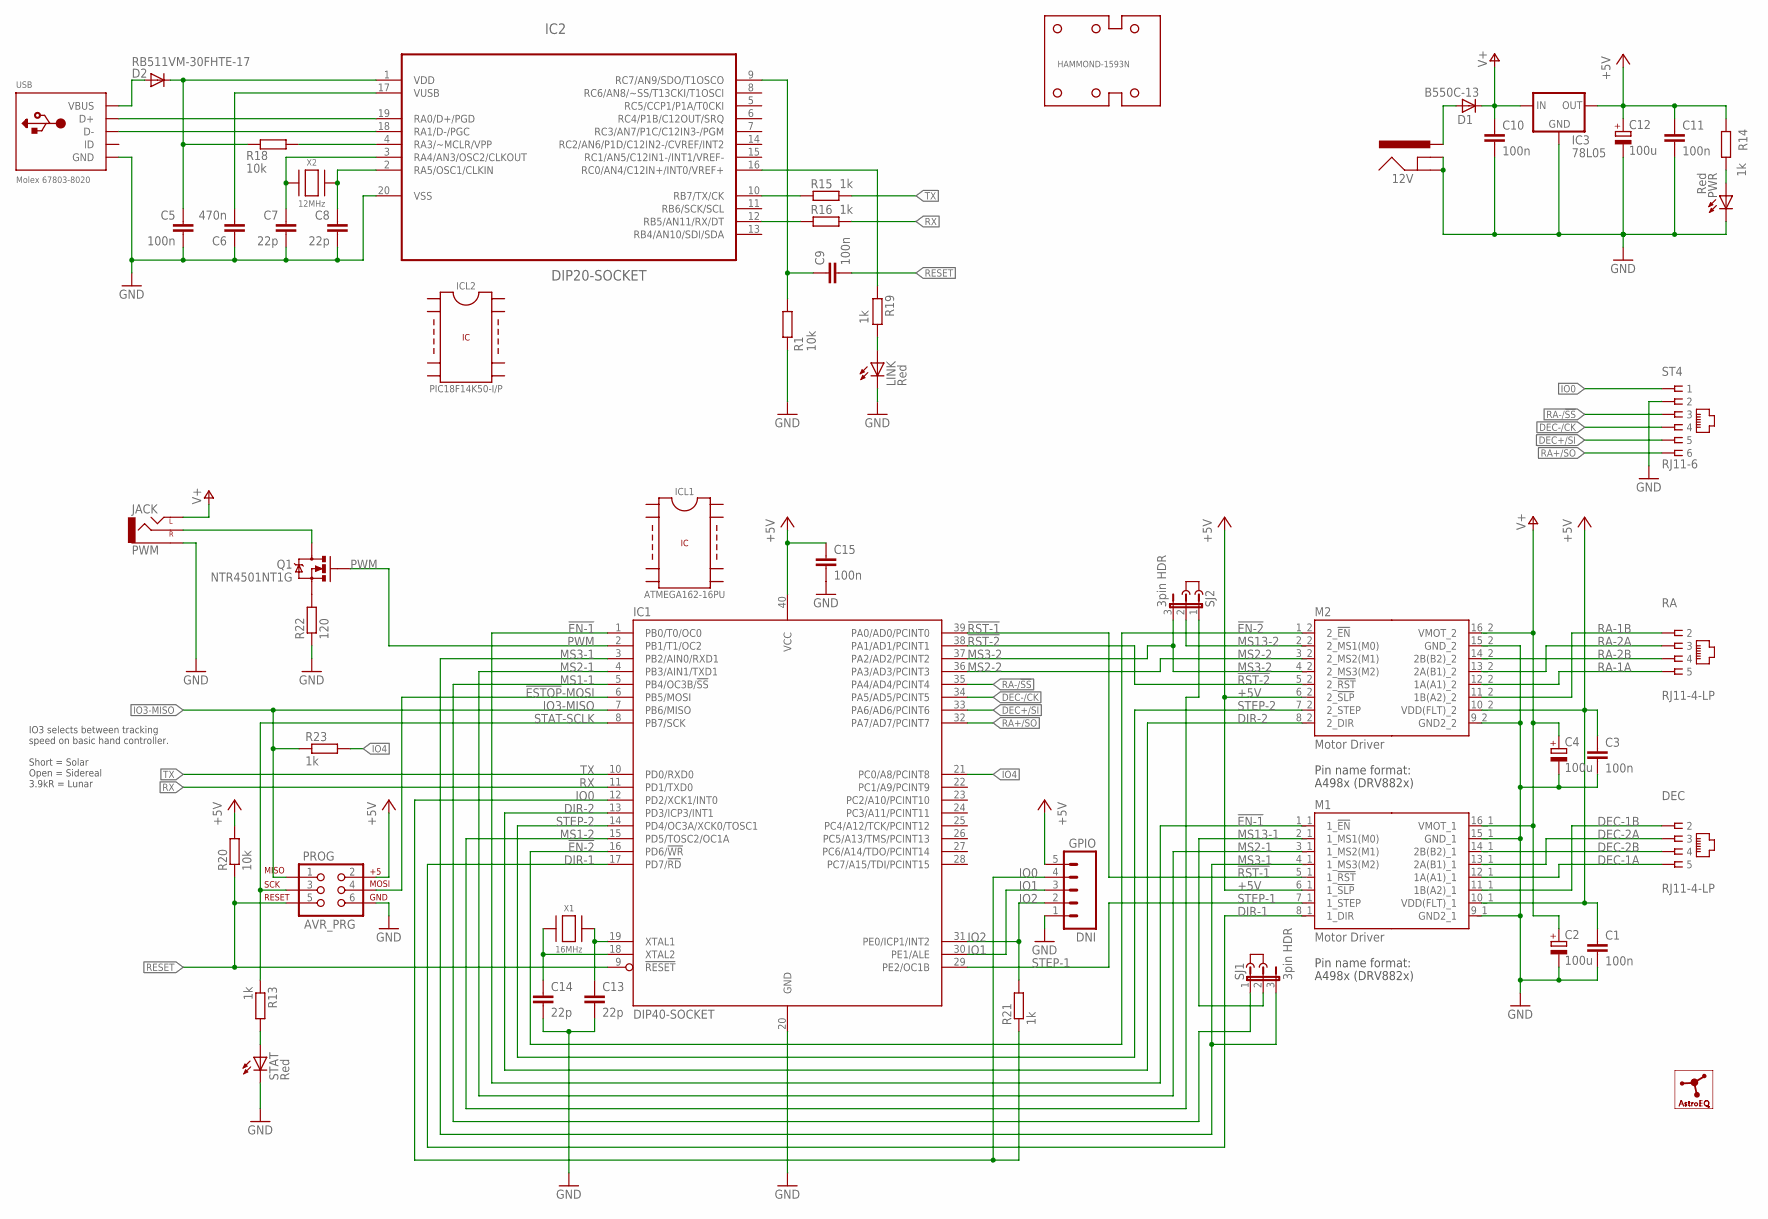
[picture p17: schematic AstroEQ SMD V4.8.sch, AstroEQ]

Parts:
12V: POWER_JACKPTH; POWER_JACK_PTH; MPN MJ-179PH
C1, C3, C5, C9, C10, C11, C15: 100n; C0603; MPN MC0603F104Z250CT
C2, C4, C12: 100u; PANASONIC_D; MPN 865080545012
C6: 470n; C0603; MPN MC0603F474Z160CT
C7, C8, C13, C14: 22p; C0603; MPN MC0603N220J500CT
D1: B550C-13; SMC; MPN B550C-13-F
D2: RB511VM-30FHTE-17; SOD-323; MPN RB511VM-30FHTE-17
DEC: RJ11-4-LP; RJ11-NO_SHIELD-4-LP; MPN 95501-2641
GPIO: DNI; 1X05
HAMMOND-1593N: HAMMOND-1593N-4HOLE; HAMMOND-1593N4HOLES; MPN 1593NBK
IC1: DIP40-SOCKET; DIL40; MPN 2227MC-40-06-05-F1
IC2: DIP20-SOCKET; DIL20-SKT
IC3: 78L05; SOT89; MPN L78L05ACUTR
ICL1: ATMEGA162-16PU; IC; MPN ATMEGA162-16PU
ICL2: PIC18F14K50-I/P; IC; MPN PIC18F14K50-I/P
J2, J3: DNI; JUMP; MPN 969102-0000-DA
LINK: Red; SML1206-SIDE; MPN 155124RS73200
LOGO1: DNI; ASTROEQ-SMALL
M1: Motor Driver; CARRIER-HV-DUAL; MPN CES-116-01-T-S
M2: Motor Driver; CARRIER-LV-DUAL; MPN CES-116-01-T-S
PROG: AVR_PRG; 2X3; MPN M20-9980346
PWM: JACK; AUDIO-JACK; MPN FC68131
PWR: Red; SML1206-SIDE; MPN 155124RS73200
Q1: NTR4501NT1G; SOT23-3; MPN NTR4501NT1G
R1, R18, R20: 10k; R0603; MPN MCWR06X1002FTL
R13, R14, R15, R16, R19, R21, R23: 1k; R0603; MPN MCWR06X1001FTL
R22: 120; R0805; MPN MCWR08X1200FTL
RA: RJ11-4-LP; RJ11-NO_SHIELD-4-LP; MPN 95501-2641
SJ1, SJ2: 3pin HDR; JP2; MPN M20-9990345.
ST4: RJ11-6; RJ11-NO_SHIELD-LP; MPN 95501-2661
STAT: Red; SML1206-SIDE; MPN 155124RS73200
USB: Molex 67803-8020; USB-MINIAB; MPN 67803-8020
X1: 16MHz; NX5032; MPN 7A-16.000MAAJ-T
X2: 12MHz; NX5032; MPN 7A-12.000MAAJ-T

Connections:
!EN-1: IC1.1 (PB0/T0/OC0), M2.1_1 (1_!EN)
!EN-2: IC1.16 (PD6/!WR), M2.1_2 (2_!EN)
!ESTOP!-MOSI: IC1.6 (PB5/MOSI), PROG.4
!RST-1: IC1.39 (PA0/AD0/PCINT0), M2.5_1 (1_!RST)
!RST-2: IC1.38 (PA1/AD1/PCINT1), M2.5_2 (2_!RST)
+5V: C1.1, C3.1, C11.1, C12.+, C15.1, GPIO.5, IC1.40 (VCC), IC3.1 (OUT), M1.10_1 (VDD(FLT)_1), M1.10_2 (VDD(FLT)_2), M2.6_1 (1_!SLP), M2.6_2 (2_!SLP), PROG.2, R14.1, R20.2
AVROSC1: C13.1, IC1.19 (XTAL1), X1.P$2
AVROSC2: C14.1, IC1.18 (XTAL2), X1.P$1
DEC+/SI: IC1.33 (PA6/AD6/PCINT6), ST4.5
DEC-1A: DEC.5, M1.12_1 (1A(A1)_1)
DEC-1B: DEC.2, M1.11_1 (1B(A2)_1)
DEC-2A: DEC.3, M1.13_1 (2A(B1)_1)
DEC-2B: DEC.4, M1.14_1 (2B(B2)_1)
DEC-/CK: IC1.34 (PA5/AD5/PCINT5), ST4.4
DIR-1: IC1.17 (PD7/!RD), M2.8_1 (1_DIR)
DIR-2: IC1.13 (PD3/ICP3/INT1), M2.8_2 (2_DIR)
DTR: C9.1, IC2.9 (RC7/AN9/SDO/T1OSCO), R1.1
D_N: IC2.18 (RA1/D-/PGC), USB.D-
D_P: IC2.19 (RA0/D+/PGD), USB.D+
GND: 12V.GND, 12V.GNDBREAK, C1.2, C2.-, C3.2, C4.-, C5.2, C6.1, C7.2, C8.2, C10.2, C11.2, C12.-, C13.2, C14.2, C15.2, GPIO.1, IC1.20 (GND), IC2.20 (VSS), IC3.2 (GND), IC3.4 (GND), LINK.C, LINK.E (C), M1.9_1 (GND2_1), M1.9_2 (GND2_2), M1.15_1 (GND_1), M1.15_2 (GND_2), PROG.6, PWM.SLEEVE, PWR.C, PWR.E (C), R1.2, R22.1, ST4.2, STAT.C, STAT.E (C), USB.GND, USB.GND1 (GND), USB.GND2 (GND), USB.GND3 (GND), USB.GND4 (GND)
IO0: GPIO.4, IC1.12 (PD2/XCK1/INT0), R21.1, ST4.1
IO1: GPIO.3, IC1.30 (PE1/ALE)
IO2: GPIO.2, IC1.31 (PE0/ICP1/INT2), R21.2
IO3-MISO: IC1.7 (PB6/MISO), PROG.1, R23.1
IO4: IC1.21 (PC0/A8/PCINT8), R23.2
MCLR: IC2.4 (RA3/~MCLR/VPP), R18.1
MS1-1: IC1.5 (PB4/OC3B/!SS), SJ1.1
MS1-2: IC1.15 (PD5/TOSC2/OC1A), SJ2.1
MS2-1: IC1.4 (PB3/AIN1/TXD1), M2.3_1 (1_MS2(M1))
MS2-2: IC1.36 (PA3/AD3/PCINT3), M2.3_2 (2_MS2(M1))
MS3-1: IC1.3 (PB2/AIN0/RXD1), M2.4_1 (1_MS3(M2)), SJ1.3
MS3-2: IC1.37 (PA2/AD2/PCINT2), M2.4_2 (2_MS3(M2)), SJ2.3
MS13-1: M2.2_1 (1_MS1(M0)), SJ1.2
MS13-2: M2.2_2 (2_MS1(M0)), SJ2.2
PWM: IC1.2 (PB1/T1/OC2), Q1.1 (G)
PWM-ILIM: Q1.2 (S), R22.2
PWM-OD: PWM.RING (RIGHT), Q1.3 (D)
PWRLED: PWR.A, R14.2
RA+/SO: IC1.32 (PA7/AD7/PCINT7), ST4.6
RA-1A: M1.12_2 (1A(A1)_2), RA.5
RA-1B: M1.11_2 (1B(A2)_2), RA.2
RA-2A: M1.13_2 (2A(B1)_2), RA.3
RA-2B: M1.14_2 (2B(B2)_2), RA.4
RA-/!SS: IC1.35 (PA4/AD4/PCINT4), ST4.3
RESET: C9.2, IC1.9 (!RESET), PROG.5, R20.1
RX: IC1.11 (PD1/TXD0), R16.1
RX(USB): IC2.12 (RB5/AN11/RX/DT), R16.2
STAT-SCLK: IC1.8 (PB7/SCK), PROG.3, R13.1
STATLED: R13.2, STAT.A
STEP-1: IC1.29 (PE2/OC1B), M2.7_1 (1_STEP)
STEP-2: IC1.14 (PD4/OC3A/XCK0/TOSC1), M2.7_2 (2_STEP)
TX: IC1.10 (PD0/RXD0), R15.1
TX(USB): IC2.10 (RB7/TX/CK), R15.2
USBLED: LINK.A, R19.1
USBOSC1: C8.1, IC2.2 (RA5/OSC1/CLKIN), X2.P$2
USBOSC2: C7.1, IC2.3 (RA4/AN3/OSC2/CLKOUT), X2.P$1
USBSTAT: IC2.16 (RC0/AN4/C12IN+/INT0/VREF+), R19.2
V+: C2.+, C4.+, C10.1, D1.C, IC3.3 (IN), M1.16_1 (VMOT_1), M1.16_2 (VMOT_2), PWM.TIP (LEFT)
VBUS: D2.2 (A), USB.VBUS
VIN: 12V.PWR, D1.A
VPIC: C5.1, D2.1 (C), IC2.1 (VDD), R18.2
VUSB: C6.2, IC2.17 (VUSB)

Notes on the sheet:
IO3 selects between tracking speed on basic hand controller. Short = Solar Open = Sidereal 3.9kR = Lunar

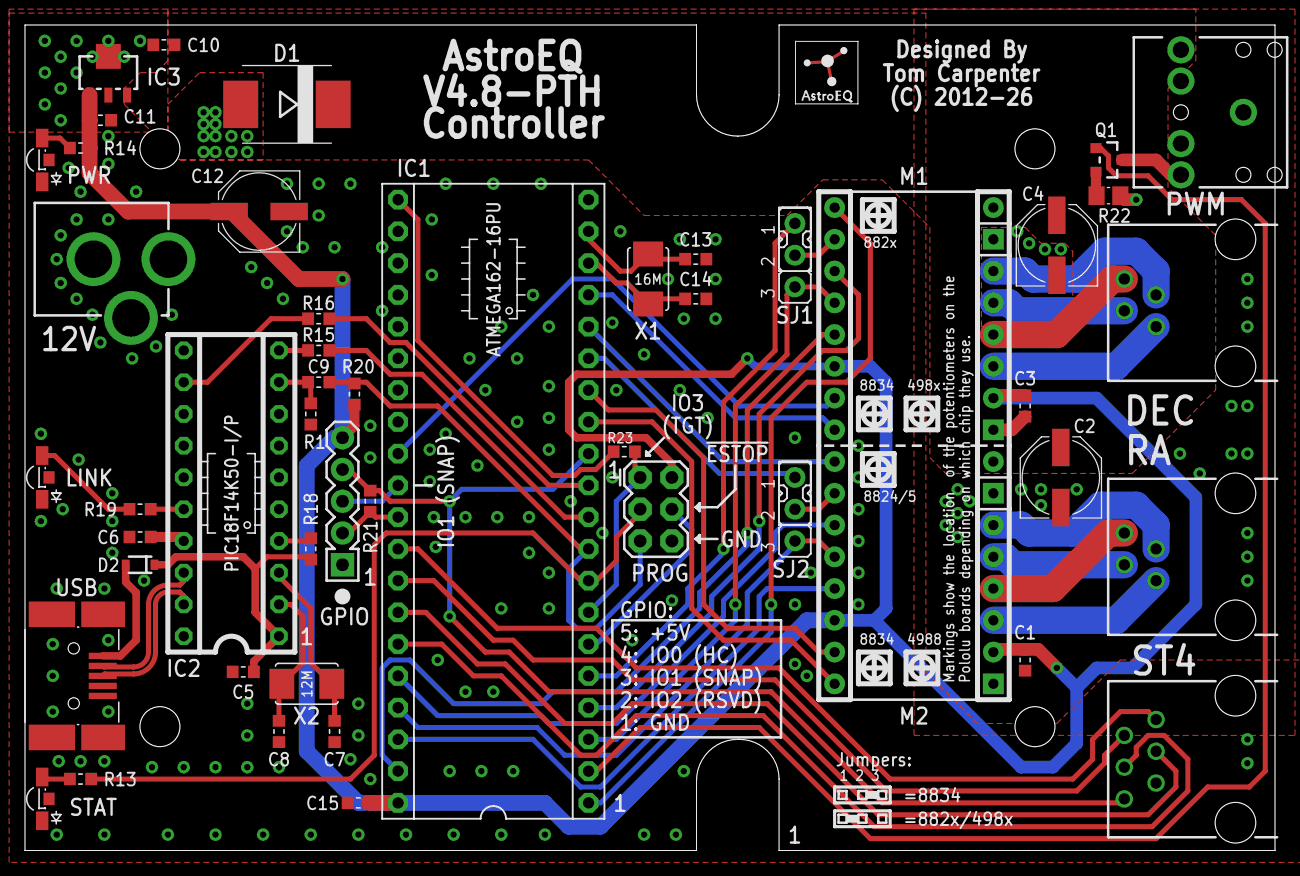
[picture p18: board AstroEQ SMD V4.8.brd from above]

Board: 2 copper layers, 100.0 x 66.0 mm, 55 parts (0 on the bottom side), 62 nets.

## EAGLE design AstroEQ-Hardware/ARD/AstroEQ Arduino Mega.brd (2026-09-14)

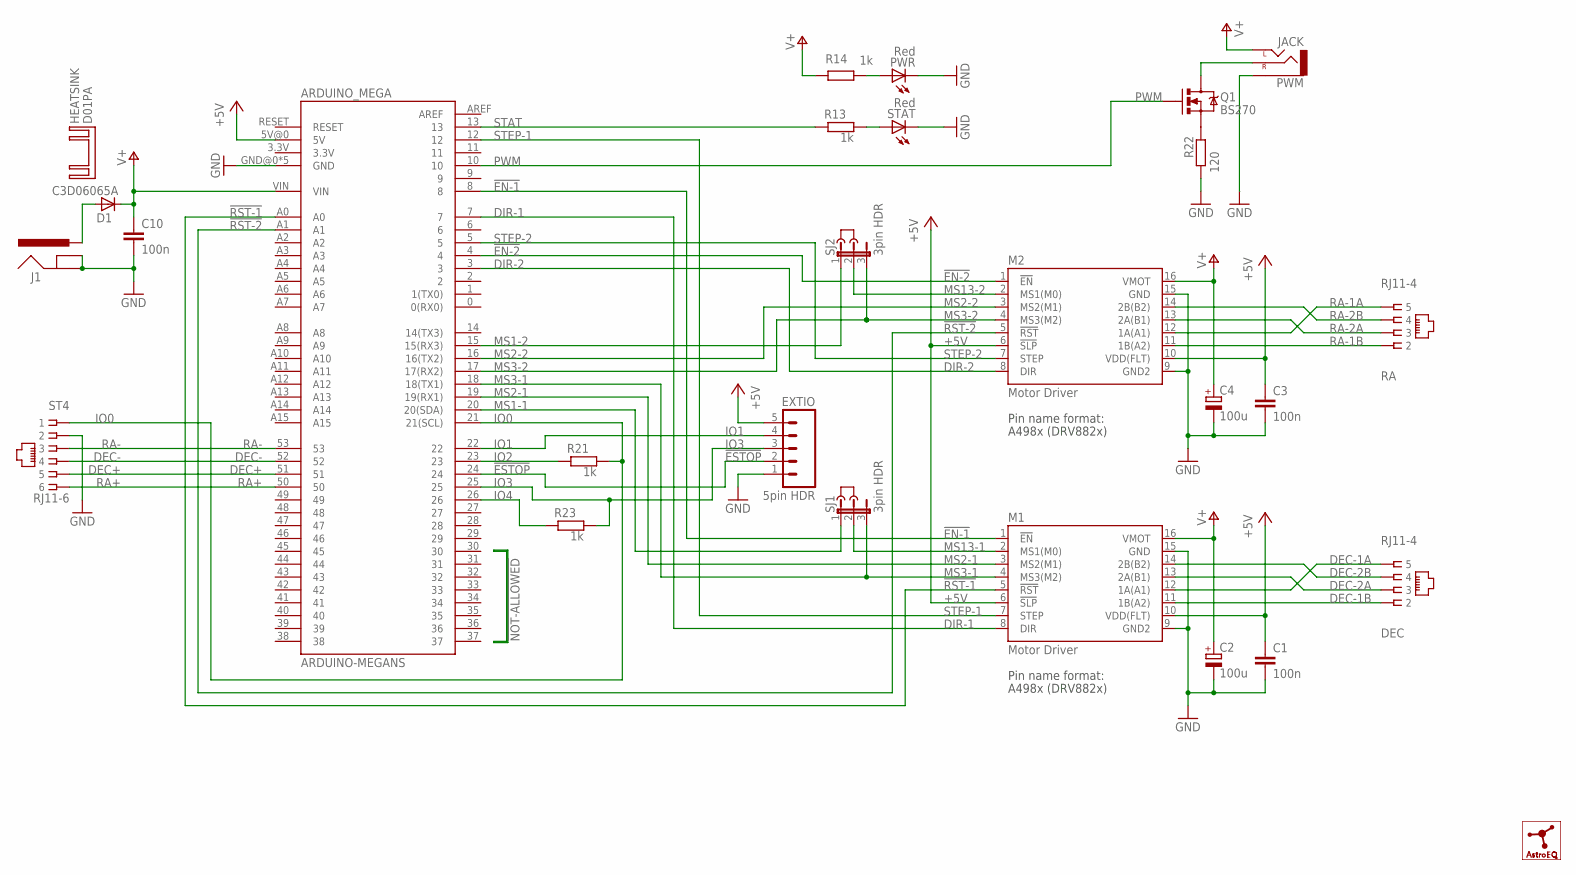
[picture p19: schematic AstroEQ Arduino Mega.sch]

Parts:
ARDUINO_MEGA: ARDUINO-MEGANS; ARDUINO_MEGA_NS
C1, C3, C10: 100n; C025-024X044; MPN SR205C104KAR
C2, C4: 100u; E2,5-7; MPN MCGPR25V107M6.3X11
D1: C3D06065A; TO220ACS; MPN C3D06065A
DEC: RJ11-4; RJ11-NO_SHIELD-4; MPN 95501-2641
EXTIO: 5pin HDR; 1X05
HEATSINK: D01PA
J1: POWER_JACKPTH; POWER_JACK_PTH; MPN MJ-179PH
J2, J3: DNI; JUMP; MPN 969102-0000-DA
LOGO1: ASTROEQ8MM; ASTROEQ
M1, M2: Motor Driver; DIP16-W; MPN CES-116-01-T-S
PWM: JACK; AUDIO-JACK-3.5MM-VERT
PWR: Red; LED3MM; MPN L-424HDT
Q1: BS270; TO-92; MPN BS270
R13: 1k; 0204/5; MPN MF12 1K
R14, R21, R23: 1k; 0204/7; MPN MF12 1K
R22: 120; 0204/7; MPN MF12 120R
RA: RJ11-4; RJ11-NO_SHIELD-4; MPN 95501-2641
SJ1, SJ2: 3pin HDR; JP2; MPN M20-9990345.
ST4: RJ11-6; RJ11-NO_SHIELD
STAT: Red; LED3MM; MPN L-424HDT

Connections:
!EN-1: ARDUINO_MEGA.8, M1.1 (!EN)
!EN-2: ARDUINO_MEGA.4, M2.1 (!EN)
!ESTOP: ARDUINO_MEGA.24, EXTIO.2
!RST-1: ARDUINO_MEGA.A0, M1.5 (!RST)
!RST-2: ARDUINO_MEGA.A1, M2.5 (!RST)
+5V: ARDUINO_MEGA.5V@0 (5V), C1.1, C3.1, EXTIO.5, M1.6 (!SLP), M1.10 (VDD(FLT)), M2.6 (!SLP), M2.10 (VDD(FLT))
DEC+: ARDUINO_MEGA.51, ST4.5
DEC-: ARDUINO_MEGA.52, ST4.4
DEC-1A: DEC.5, M1.12 (1A(A1))
DEC-1B: DEC.2, M1.11 (1B(A2))
DEC-2A: DEC.3, M1.13 (2A(B1))
DEC-2B: DEC.4, M1.14 (2B(B2))
DIR-1: ARDUINO_MEGA.7, M1.8 (DIR)
DIR-2: ARDUINO_MEGA.3, M2.8 (DIR)
GND: ARDUINO_MEGA.GND@0 (GND), ARDUINO_MEGA.GND@1 (GND), ARDUINO_MEGA.GND@2 (GND), ARDUINO_MEGA.GND@3 (GND), ARDUINO_MEGA.GND@4 (GND), C1.2, C2.-, C3.2, C4.-, C10.2, EXTIO.1, J1.GND, J1.GNDBREAK, M1.9 (GND2), M1.15 (GND), M2.9 (GND2), M2.15 (GND), PWM.1 (SLEEVE), PWR.K (C), R22.1, ST4.2, STAT.K (C)
IO0: ARDUINO_MEGA.21 (21(SCL)), R21.2, ST4.1
IO1: ARDUINO_MEGA.22, EXTIO.4
IO2: ARDUINO_MEGA.23, R21.1
IO3: ARDUINO_MEGA.25, EXTIO.3, R23.2
IO4: ARDUINO_MEGA.26, R23.1
MS1-1: ARDUINO_MEGA.20 (20(SDA)), SJ1.1
MS1-2: ARDUINO_MEGA.15 (15(RX3)), SJ2.1
MS2-1: ARDUINO_MEGA.19 (19(RX1)), M1.3 (MS2(M1))
MS2-2: ARDUINO_MEGA.16 (16(TX2)), M2.3 (MS2(M1))
MS3-1: ARDUINO_MEGA.18 (18(TX1)), M1.4 (MS3(M2)), SJ1.3
MS3-2: ARDUINO_MEGA.17 (17(RX2)), M2.4 (MS3(M2)), SJ2.3
MS13-1: M1.2 (MS1(M0)), SJ1.2
MS13-2: M2.2 (MS1(M0)), SJ2.2
PWM: ARDUINO_MEGA.10, Q1.2 (G)
PWM-ILIM: Q1.3 (S), R22.2
PWM-OUT: PWM.3 (RIGHT), Q1.1 (D)
PWRLED: PWR.A, R14.2
RA+: ARDUINO_MEGA.50, ST4.6
RA-: ARDUINO_MEGA.53, ST4.3
RA-1A: M2.12 (1A(A1)), RA.5
RA-1B: M2.11 (1B(A2)), RA.2
RA-2A: M2.13 (2A(B1)), RA.3
RA-2B: M2.14 (2B(B2)), RA.4
STAT: ARDUINO_MEGA.13, R13.1
STATLED: R13.2, STAT.A
STEP-1: ARDUINO_MEGA.12, M1.7 (STEP)
STEP-2: ARDUINO_MEGA.5, M2.7 (STEP)
V+: ARDUINO_MEGA.VIN, C2.+, C4.+, C10.1, D1.C, M1.16 (VMOT), M2.16 (VMOT), PWM.2 (LEFT), R14.1
VIN: D1.A, J1.PWR

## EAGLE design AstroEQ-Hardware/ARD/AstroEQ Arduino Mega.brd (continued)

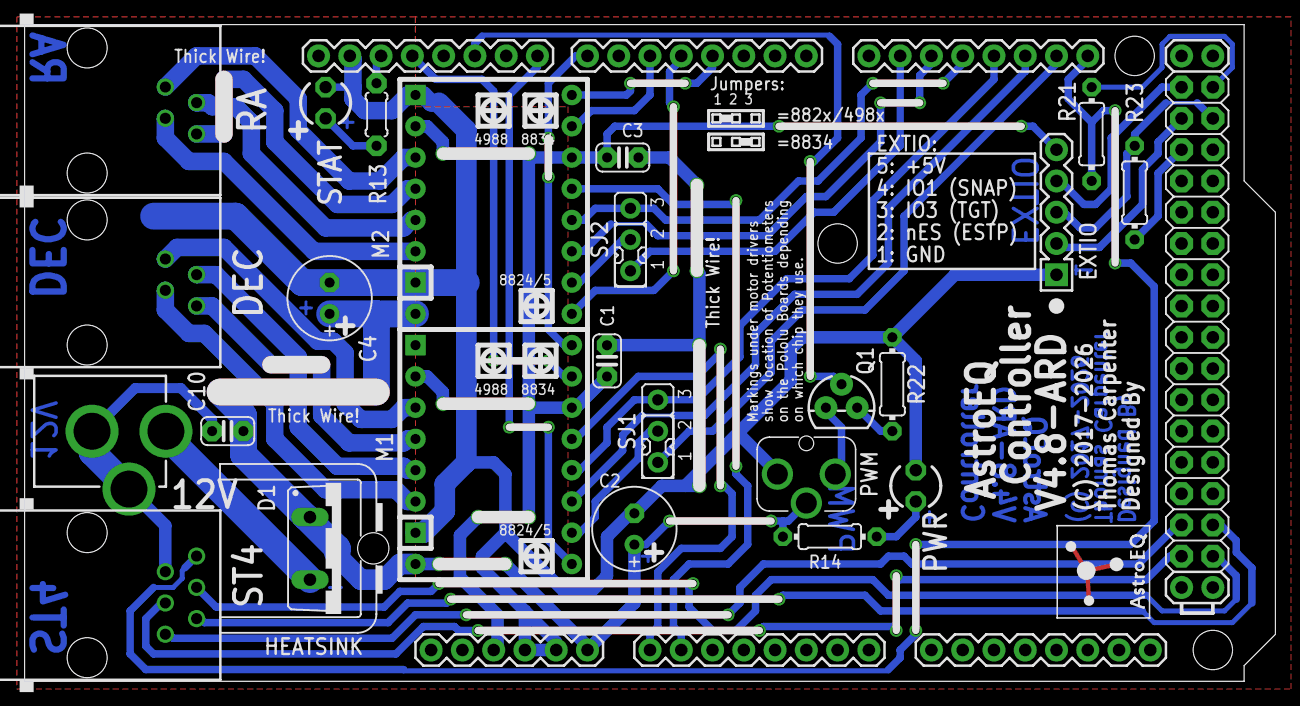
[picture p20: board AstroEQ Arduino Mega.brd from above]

Board: 2 copper layers, 101.6 x 53.3 mm, 29 parts (0 on the bottom side), 44 nets.

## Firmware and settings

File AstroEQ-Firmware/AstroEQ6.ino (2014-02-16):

/*
  Code written by Thomas Carpenter 2012
  
  With thanks Chris over at the EQMOD Yahoo group for explaining the Skywatcher protocol
  
  
  Equatorial mount tracking system for integration with EQMOD using the Skywatcher/Syntia
  communication protocol.
 
  Works with EQ5, HEQ5, and EQ6 mounts
 
  Current Verison: 7.0
*/

//Only works with ATmega162, and Arduino Mega boards (1280 and 2560)
#if defined(__AVR_ATmega162__) || defined(__AVR_ATmega1280__) || defined(__AVR_ATmega2560__)

#include "synta.h" //Synta Communications Protocol.
#include "PinMappings.h" //Read Pin Mappings
#include "EEPROMReader.h" //Read config file
#include "EEPROMAddresses.h" //Config file addresses
#include <util/delay.h>

Synta synta = Synta::getInstance(1281); //create a mount instance, specify version!

#define RA 0 //Right Ascension is AstroEQ axis 0 (Synta axis '1')
#define DC 1 //Declination is AstroEQ axis 1 (Synta axis '2')

//#define DEBUG 1
byte stepIncrement[2];
unsigned int normalGotoSpeed[2];
unsigned int gotoFactor[2];
unsigned int minSpeed[2];
unsigned int stopSpeed[2];
byte readyToGo[2] = {0,0};
volatile byte gotoRunning[2] = {0,0};
unsigned long gotoPosn[2] = {0UL,0UL}; //where to slew to

#define timerCountRate 8000000

#define NormalDistnWidth 32
#define HighspeedDistnWidth 4
unsigned int timerOVF[2][max(HighspeedDistnWidth,NormalDistnWidth)];
boolean highSpeed[2] = {false,false};
byte distributionWidth[2] = {NormalDistnWidth,NormalDistnWidth};
byte stepIncrementRepeat[2] = {0,0};
unsigned int gotoDecelerationLength[2];
#define distributionSegment(m) (m ? GPIOR1 : GPIOR0) 
#define decelerationStepsLow(m) (m ? EEDR : DDRC)
#define decelerationStepsHigh(m) (m ? EEARL : PORTC)
#define currentMotorSpeed(m) (m ? OCR3A : OCR3B)
#define interruptCount(m) (m ? OCR1A : OCR1B)
#define interruptOVFCount(m) (m ? ICR3 : ICR1)
#define interruptControlRegister(m) (m ? TIMSK3 : TIMSK1)
#define interruptControlBitMask(m) (m ? _BV(ICIE3) : _BV(ICIE1))
#define timerCountRegister(m) (m ? TCNT3 : TCNT1)
#define timerPrescalarRegister(m) (m ? TCCR3B : TCCR1B)

//Pins
const byte statusPin = statusPin_Define;
const byte resetPin[2] = {resetPin_0_Define,resetPin_1_Define};
const byte dirPin[2] = {dirPin_0_Define,dirPin_1_Define};
const byte enablePin[2] = {enablePin_0_Define,enablePin_1_Define};
const byte stepPin[2] = {stepPin_0_Define,stepPin_1_Define};
const byte st4Pin[2][2] = {{ST4AddPin_0_Define,ST4SubPin_0_Define},{ST4AddPin_1_Define,ST4SubPin_1_Define}};

#ifdef LEGACY_MODE
const byte modePins[2][2] = {{modePins0_0_Define,modePins2_0_Define},{modePins0_1_Define,modePins2_1_Define}};
#else
const byte modePins[2][3] = {{modePins0_0_Define,modePins1_0_Define,modePins2_0_Define},{modePins0_1_Define,modePins1_1_Define,modePins2_1_Define}};
#endif
 

byte encodeDirection[2];

#define _STEP0_HIGH _BV(digitalPinToBit(stepPin[RA]))
#define _STEP0_LOW (~_STEP0_HIGH)
#define STEP0PORT *digitalPinToPortReg(stepPin[RA])
#define _STEP1_HIGH _BV(digitalPinToBit(stepPin[DC]))
#define _STEP1_LOW (~_STEP1_HIGH)
#define STEP1PORT *digitalPinToPortReg(stepPin[DC])
#define stepPort(m) (m ? STEP1PORT : STEP0PORT)
#define stepHigh(m) (m ? _STEP1_HIGH : _STEP0_HIGH)
#define stepLow(m) (m ? _STEP1_LOW : _STEP0_LOW)

#ifdef LEGACY_MODE
byte modeState[2][2] = {{HIGH,HIGH},{LOW,LOW}};
#define MODE0 0
#define MODE2 1
#define STATE16 0
#define STATE2 1
#else
byte modeState[2][3] = {{HIGH,HIGH,HIGH},{HIGH,LOW,LOW}};
#define MODE0 0
#define MODE1 1
#define MODE2 2
#define STATE16 0
#define STATE2 1

#endif

boolean checkEEPROM(){
  char temp[9] = {0};
  EEPROM.readString(temp,8,AstroEQID_Address);
  return !(strncmp(temp,"AstroEQ",8));
}

void systemInitialiser(){
  encodeDirection[RA] = EEPROM.readByte(RAReverse_Address);  //reverse the right ascension if 1
  encodeDirection[DC] = EEPROM.readByte(DECReverse_Address); //reverse the declination if 1
  

#ifdef LEGACY_MODE
  //modeState[STATE2][MODE0] =  EEPROM.readByte(Driver_Address);
  //modeState[STATE16][MODE0] = !modeState[STATE2][MODE0];
  modeState[STATE2][MODE0] =  EEPROM.readByte(Driver_Address);
#else
  //modeState[STATE16][MODE1] = !EEPROM.readByte(Driver_Address);
  //modeState[STATE16][MODE0] = modeState[STATE16][MODE1];
  modeState[STATE16][MODE0] = !EEPROM.readByte(Driver_Address);
  modeState[STATE2][MODE0] = modeState[STATE16][MODE0];
  modeState[STATE2][MODE1] = !modeState[STATE16][MODE0];
#endif
  
  unsigned int multiplierRA = synta.cmd.siderealIVal[RA]/75;
  unsigned int multiplierDC = synta.cmd.siderealIVal[DC]/75;
  gotoFactor[RA] = EEPROM.readByte(RAGoto_Address);
  normalGotoSpeed[RA] = multiplierRA * gotoFactor[RA] + 1;
  gotoFactor[DC] = EEPROM.readByte(DECGoto_Address);
  normalGotoSpeed[DC] = multiplierDC * gotoFactor[DC] + 1;
  
  highSpeed[RA] = !EEPROM.readByte(Microstep_Address);
  highSpeed[DC] = highSpeed[RA];
  distributionWidth[RA] = highSpeed[RA] ? HighspeedDistnWidth : NormalDistnWidth;
  distributionWidth[DC] = highSpeed[DC] ? HighspeedDistnWidth : NormalDistnWidth;
  
#ifdef DEBUG
  Serial1.println();
  Serial1.println(minSpeed[RA]);
  Serial1.println(minSpeed[DC]);
  Serial1.println();
  Serial1.println(normalGotoSpeed[RA]);
  Serial1.println(normalGotoSpeed[DC]);
  Serial1.println();
  Serial1.println(multiplierRA);
  Serial1.println(multiplierDC);
  Serial1.println();
#endif
  if(!checkEEPROM()){
    while(1); //prevent AstroEQ startup if EEPROM is blank.
  }
  minSpeed[RA] = synta.cmd.siderealIVal[RA]>>1;//2x sidereal rate.
  minSpeed[DC] = synta.cmd.siderealIVal[DC]>>1;//[minspeed is the point at which acceleration curves are enabled]
  calculateRate(RA); //Initialise the interrupt speed table. This now only has to be done once at the beginning.
  calculateRate(DC); //Initialise the interrupt speed table. This now only has to be done once at the beginning.
  gotoDecelerationLength[RA] = calculateDecelerationLength(RA);
  gotoDecelerationLength[DC] = calculateDecelerationLength(DC);
}

unsigned int calculateDecelerationLength (byte axis){
  unsigned int currentSpeed = normalGotoSpeed[axis];
  unsigned int stoppingSpeed = minSpeed[axis];
  unsigned int stepRepeat = synta.cmd.stepRepeat[axis] + 1;
  unsigned int numberOfSteps = 0;
  while(currentSpeed < stoppingSpeed) {
    currentSpeed += (currentSpeed >> 5) + 1; //work through the decelleration formula.
    numberOfSteps += stepRepeat; //n more steps
  }
  //number of steps now contains how many steps required to slow to a stop.
  if (!(numberOfSteps & 0xFF)) {
    numberOfSteps++; //If it is a multiple of 16, an assumption in the ISR calculations won't hold true. So add an extra step.
  }
  return numberOfSteps;
}

int main(void)
{
  sei();
#ifdef DEBUG
  Serial1.begin(115200);
#endif
  systemInitialiser();
  
#if defined(__AVR_ATmega162__)
  //Timer 2 registers are being used as general purpose data storage for high efficency interrupt routines. So timer must be fully disabled.
  TCCR2 = 0;
  ASSR=0;
#endif
  
  pinMode(statusPin,OUTPUT);
  for(byte i = 0;i < 2;i++){ //for each motor...
    pinMode(enablePin[i],OUTPUT); //enable the Enable pin
    digitalWrite(enablePin[i],HIGH); //IC disabled
    pinMode(stepPin[i],OUTPUT); //enable the step pin
    digitalWrite(stepPin[i],LOW); //default is low
    pinMode(dirPin[i],OUTPUT); //enable the direction pin
    digitalWrite(dirPin[i],LOW); //default is low
    const byte* modePin = modePins[i];
    const byte* state = modeState[highSpeed[i]];
#ifdef LEGACY_MODE
    for(byte j = 0; j < 2; j++){
      pinMode(modePin[j],OUTPUT);
      digitalWrite(modePin[j],state[j]);
    }
#else
    for(byte j = 0; j < 3; j++){
      pinMode(modePin[j],OUTPUT);
      digitalWrite(modePin[j],state[j]);
    }
#endif
    pinMode(resetPin[i],OUTPUT); //enable the reset pin
    digitalWrite(resetPin[i],LOW); //active low reset
    _delay_ms(1); //allow ic to reset
    digitalWrite(resetPin[i],HIGH); //complete reset
    
    pinMode(st4Pin[i][0],INPUT_PULLUP);
    pinMode(st4Pin[i][1],INPUT_PULLUP);
  }
    
  // start Serial port:
  Serial.begin(9600); //SyncScan runs at 9600Baud, use a serial port of your choice 
  while(Serial.available()){
    Serial.read(); //Clear the buffer
  }
  
  //setup interrupt for ST4 connection
#if defined(__AVR_ATmega162__)
  PCMSK0 = 0xF0; //PCINT[4..7]
#define PCICR GICR
#else
  PCMSK0 = 0x0F; //PCINT[0..3]
  PCICR &= ~_BV(PCIE2); //disable PCInt[16..23] vector
#endif
  PCICR &= ~_BV(PCIE1); //disable PCInt[8..15] vector
  PCICR |= _BV(PCIE0); //enable PCInt[0..7] vector

  for(;;){ //loop
    //static unsigned long lastMillis = millis();
    //static boolean isLedOn = false;
    char decodedPacket[11]; //temporary store for completed command ready to be processed
    //*digitalPinToPortReg(statusPin) &= ~_BV(digitalPinToBit(statusPin));
    if (Serial.available()) { //is there a byte in buffer
      *digitalPinToPortReg(statusPin) ^= _BV(digitalPinToBit(statusPin));
      //digitalWrite(statusPin,HIGH); //Turn on the LED to indicate activity.
      char recievedChar = Serial.read(); //get the next character in buffer
  #ifdef DEBUG
      Serial1.write(recievedChar);
  #endif
      char decoded = synta.recieveCommand(decodedPacket,recievedChar); //once full command packet recieved, decodedPacket returns either error packet, or valid packet
      if (decoded == 1){ //Valid Packet
        decodeCommand(synta.command(),decodedPacket); //decode the valid packet
      } else if (decoded == -1){ //Error
        Serial.print(decodedPacket); //send the error packet (recieveCommand() already generated the error packet, so just need to send it)
  #ifdef DEBUG
        Serial1.print(F(" ->Res:"));
        Serial1.println(decodedPacket);
  #endif
      } //otherwise command not yet fully recieved, so wait for next byte
  //    lastMillis = millis();
  //    isLedOn = true;
  //  }
  //  if (isLedOn && (millis() > lastMillis + 20)){
  //    isLedOn = false;
  //    digitalWrite(statusPin,LOW); //Turn LED back off after a short delay.
    }
    for(byte axis = 0; axis < 2; axis++){
      if(readyToGo[axis]==1){
        /*byte currentDir;
        if(synta.cmd.stepDir[axis] > 0){
          currentDir = 0;
        } else {
          currentDir = 1;
        } //convert step direction back to synta direction.
        
        //If directions are the same, we can just continue and decellerate to target speed.
        */
        //if motor is stopped, then we can accelerate to target speed.
        //Otherwise don't start the next movement until we have stopped.
        if(/*(currentDir == synta.cmd.dir[axis]) || */(synta.cmd.stopped[axis])){
          synta.cmd.updateStepDir(axis);
          if(synta.cmd.GVal[axis] & 1){
            //This is the funtion that enables a slew type move.
            slewMode(axis); //Slew type
            readyToGo[axis] = 2;
          } else {
            //This is the function for goto mode. You may need to customise it for a different motor driver
            gotoMode(axis); //Goto Mode
            readyToGo[axis] = 0;
          }
        }
      }
    }
  #ifdef DEBUG
    if (Serial1.available()) { //is there a byte in buffer
      Serial1.println();
      Serial1.println(currentMotorSpeed(RA));
      Serial1.println(currentMotorSpeed(DC));
      Serial1.println(interruptOVFCount(RA));
      Serial1.println(interruptOVFCount(DC));
      Serial1.println();
      Serial1.read();
    }
  #endif
  }
}

void decodeCommand(char command, char* packetIn){ //each command is axis specific. The axis being modified can be retrieved by calling synta.axis()
  char response[11]; //generated response string
  unsigned long responseData = 0; //data for response
  byte axis = synta.axis();
  unsigned int correction;
  //byte scalar = synta.scalar[axis]+1;
  uint8_t oldSREG;
  switch(command){
    case 'e': //readonly, return the eVal (version number)
        responseData = synta.cmd.eVal[axis]; //response to the e command is stored in the eVal function for that axis.
        break;
    case 'a': //readonly, return the aVal (steps per axis)
        responseData = synta.cmd.aVal[axis]; //response to the a command is stored in the aVal function for that axis.
        break;
    case 'b': //readonly, return the bVal (sidereal step rate)
        responseData = synta.cmd.bVal[axis]; //response to the b command is stored in the bVal function for that axis.
        correction = (synta.cmd.siderealIVal[axis] << 1);
        responseData = (responseData * (correction+1))/correction; //account for rounding inside Skywatcher DLL.
        break;
    case 'g': //readonly, return the gVal (high speed multiplier)
        responseData = synta.cmd.gVal[axis]; //response to the g command is stored in the gVal function for that axis.
        break;
    case 's': //readonly, return the sVal (steps per worm rotation)
        responseData = synta.cmd.sVal[axis]; //response to the s command is stored in the sVal function for that axis.
        break;
    case 'f': //readonly, return the fVal (axis status)
        responseData = synta.cmd.fVal(axis); //response to the f command is stored in the fVal function for that axis.
        break;
    case 'j': //readonly, return the jVal (current position)
        oldSREG = SREG; 
        cli();  //The next bit needs to be atomic, just in case the motors are running
        responseData = synta.cmd.jVal[axis]; //response to the j command is stored in the jVal function for that axis.
        SREG = oldSREG;
        break;
    case 'K': //stop the motor, return empty response
        motorStop(axis,0); //normal ISR based decelleration trigger.
        readyToGo[axis] = 0;
        break;
    case 'L':
        motorStop(axis,1); //emergency axis stop.
        motorDisable(axis); //shutdown driver power.
        break;
    case 'G': //set mode and direction, return empty response
        if (packetIn[0] == '0'){
          packetIn[0] = '2'; //don't allow a high torque goto. But do allow a high torque slew.
        }
        synta.cmd.setGVal(axis, (packetIn[0] - '0')); //Store the current mode for the axis
        synta.cmd.setDir(axis, (packetIn[1] - '0')); //Store the current direction for that axis
        readyToGo[axis] = 0;
        break;
    case 'H': //set goto position, return empty response (this sets the number of steps to move from cuurent position if in goto mode)
        synta.cmd.setHVal(axis, synta.hexToLong(packetIn)); //set the goto position container (convert string to long first)
        readyToGo[axis] = 0;
        break;
    case 'I': //set slew speed, return empty response (this sets the speed to move at if in slew mode)
        responseData = synta.hexToLong(packetIn);
        //if (responseData > minSpeed[axis]){
        //  responseData = minSpeed[axis]; //minimum speed limit <- if it is slower than this, there will be no acelleration.
        //}
        synta.cmd.setIVal(axis, responseData); //set the speed container (convert string to long first) 
        responseData = 0;
        if (readyToGo[axis] == 2){
          motorStart(axis,1); //Update Speed.
        } else {
          readyToGo[axis] = 0;
        }
        break;
    case 'E': //set the current position, return empty response
        oldSREG = SREG; 
        cli();  //The next bit needs to be atomic, just in case the motors are running
        synta.cmd.setjVal(axis, synta.hexToLong(packetIn)); //set the current position (used to sync to what EQMOD thinks is the current position at startup
        SREG = oldSREG;
        break;
    case 'F': //Enable the motor driver, return empty response
        motorEnable(axis); //This enables the motors - gives the motor driver board power
        break;
    default: //Return empty response (deals with commands that don't do anything before the response sent (i.e 'J'), or do nothing at all (e.g. 'M', 'L') )
        break;
  }
  
  synta.assembleResponse(response, command, responseData); //generate correct response (this is required as is)
  Serial.print(response); //send response to the serial port
#ifdef DEBUG

#if DEBUG == 2
  if (command != 'j')
#endif
  {
    Serial1.print(F(" ->Res:"));
    Serial1.println(response);
  }
#if DEBUG == 2
  else {
    Serial.println(); 
  }
#endif
#endif
  
  if(command == 'J'){ //J tells us we are ready to begin the requested movement. So signal we are ready to go and when the last movement complets this one will execute.
    readyToGo[axis] = 1;
    if (!(synta.cmd.GVal[axis] & 1)){
      synta.cmd.setGotoEn(axis,1);
    }
  }
}



//Calculates the rate based on the recieved I value 
void calculateRate(byte motor){
  
  unsigned long rate;
  unsigned long remainder;
  float floatRemainder;
  unsigned long divisor = synta.cmd.bVal[motor];
  byte distWidth;
 // byte GVal = synta.cmd.GVal[motor];
  //if((GVal == 2)||(GVal == 1)){ //Normal Speed}
  if(!highSpeed[motor]){ //Normal Speed
  //  highSpeed[motor] = false;
    distWidth = NormalDistnWidth;
  } else { //High Speed
  //  highSpeed[motor] = true;
    distWidth = HighspeedDistnWidth; //There are 8 times fewer steps over which to distribute extra clock cycles
  }
  
  //When dividing a very large number by a much smaller on, float accuracy is abismal. So firstly we use integer math to split the division into quotient and remainder
  rate = timerCountRate / divisor; //Calculate the quotient
  remainder = timerCountRate % divisor; //Calculate the remainder
  
  //Then convert the remainder into a decimal number (division of a small number by a larger one, improving accuracy)
  floatRemainder = (float)remainder/(float)divisor; //Convert the remainder to a decimal.
    
  //Multiply the remainder by distributionWidth to work out an approximate number of extra clocks needed per full step (each step is 'distributionWidth' microsteps)
  floatRemainder *= (float)distWidth; 
  //This many extra cycles are needed:
  remainder = (unsigned long)round(floatRemainder); 
  
  //Now truncate to an unsigned int with a sensible max value (the int is to avoid register issues with the 16 bit timer)
  if(rate > 65535UL){
    rate = 65535UL;
  } else if (rate < 128UL) {
    rate = 128UL;
  }
#if defined(__AVR_ATmega162__)
  rate--;
#endif
  
  for (byte i = 0; i < distWidth; i++){
#if defined(__AVR_ATmega162__)
    timerOVF[motor][i] = rate; //Subtract 1 as timer is 0 indexed.
#else
    timerOVF[motor][i] = rate; //Hmm, for some reason this one doesn't need 1 subtracting???
#endif
  }
  
  //evenly distribute the required number of extra clocks over the full step.
  for (unsigned long i = 0; i < remainder; i++){
    float distn = i;
    distn *= (float)distWidth;
    distn /= (float)remainder;
    byte index = (byte)ceil(distn);
    timerOVF[motor][index] += 1;
  }
  
#ifdef DEBUG
  Serial1.println();
  Serial1.println(rate);
  Serial1.println();
#endif
  
  distributionWidth[motor] = distWidth - 1; //decrement to get its bitmask. (distnWidth is always a power of 2)
  
  byte x = synta.cmd.siderealIVal[motor]>>3;
  byte y = ((unsigned int)rate)>>3;
  unsigned int divisior = x * y;
  synta.cmd.stepRepeat[motor] = (byte)((18750+(divisior>>1))/divisior)-1; //note that we are rounding to neareast so we add half the divisor.
#ifdef DEBUG
  Serial1.println();
  Serial1.println(synta.cmd.stepRepeat[motor] );
  Serial1.println();
#endif
}

void motorEnable(byte axis){
  digitalWrite(enablePin[axis],LOW);
  synta.cmd.setFVal(axis,1);
  configureTimer(); //setup the motor pulse timers.
}

void motorDisable(byte axis){
  digitalWrite(enablePin[axis],LOW);
  synta.cmd.setFVal(axis,0);
}

void slewMode(byte axis){
  motorStart(axis,1); //Begin PWM
}

void gotoMode(byte axis){
  unsigned int decelerationLength = gotoDecelerationLength[axis];
  if (axis == RA){
    if (synta.cmd.HVal[axis] < (decelerationLength>>1)){
      synta.cmd.setHVal(axis,(decelerationLength>>1));
    }
  } else {
    if (synta.cmd.HVal[axis] < 10){
      synta.cmd.setHVal(axis,10);
    }
  }
  unsigned long HVal = synta.cmd.HVal[axis];
  unsigned long halfHVal = (HVal >> 1) + 1; //make decel slightly longer than accel
  unsigned int gotoSpeed = normalGotoSpeed[axis];
  if (halfHVal < decelerationLength) {
    decelerationLength = halfHVal;
  }
#ifdef DEBUG
  Serial1.println();
  Serial1.println(decelerationLength);
  Serial1.println(synta.cmd.jVal[axis]);
#endif
  HVal -= decelerationLength;
  /*if (axis == RA){
    HVal += (decelerationLength>>2);
  }*/
  gotoPosn[axis] = synta.cmd.jVal[axis] + (synta.cmd.stepDir[axis] * HVal); //current position + relative change - decelleration region
    
#ifdef DEBUG
  Serial1.println(gotoPosn[axis]);
  Serial1.println();
#endif
  synta.cmd.setIVal(axis, gotoSpeed);
  //calculateRate(axis);
  
  motorStart(axis,decelerationLength); //Begin PWM
  gotoRunning[axis] = 1; //start the goto.
}

inline void timerEnable(byte motor, byte mode) {
  //if (mode){
    //FCPU/8
  //  timerPrescalarRegister(motor) &= ~((1<<CSn2) | (1<<CSn0)); //0x0
  //  timerPrescalarRegister(motor) |= (1<<CSn1);//x1x
  //} else {
    //FCPU/1
  timerPrescalarRegister(motor) &= ~((1<<CSn2) | (1<<CSn1));//00x
  timerPrescalarRegister(motor) |= (1<<CSn0);//xx1
  //}
  //synta.cmd.setStepLength(motor, 1);//(mode ? synta.cmd.gVal[motor] : 1));
/*#ifdef LEGACY_MODE
  for( byte j = 0; j < 2; j++){
    digitalWrite(modePins[motor][j],modeState[mode][j]);
  }
#else
  for( byte j = 0; j < 3; j++){
    digitalWrite(modePins[motor][j],modeState[mode][j]);
  }
#endif*/
}

inline void timerDisable(byte motor) {
  interruptControlRegister(motor) &= ~interruptControlBitMask(motor); //Disable timer interrupt
  timerPrescalarRegister(motor) &= ~((1<<CSn2) | (1<<CSn1) | (1<<CSn0));//00x
}

//As there is plenty of FLASH left, then to improve speed, I have created two motorStart functions (one for RA and one for DEC)
void motorStart(byte motor, unsigned int gotoDeceleration){
  if (motor == RA) {
    motorStartRA(gotoDeceleration);
  } else {
    motorStartDC(gotoDeceleration);
  }
}
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

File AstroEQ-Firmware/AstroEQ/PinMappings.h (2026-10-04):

#ifndef __PINMAPPINGS_H__
#define __PINMAPPINGS_H__

//
// Pin Mappings
//

//For custom pin map, add a copy of the #if ... #el section below,
//give it a name, e.g. titled "PIN_MAP_EXAMPLECUSTOMMAP" and add a
//commented out #define below. You can then create a pull request on
//Github if you want to share the new map.
//To use a mapping, simply uncomment the required #define. If none
//are uncommented, it will default to the standard AstroEQ mapping
//for the current AVR.

//#define PIN_MAP_EXAMPLECUSTOMMAP   //Example, copy this one to form own

#if defined(PIN_MAP_EXAMPLECUSTOMMAP)
//
//---- User Configurable Pin Definitions -----
//

//GPIO Pins:
#define gpioPin_0_Define 2   // GPIO Pin - HC Detect/Speed
#define gpioPin_1_Define 29  // Output Pin - General purpose output (EQMOD "SNAP" 1)
#define gpioPin_2_Define 28  // Control Pin - connected via 1k resistor to IO0
#define gpioPin_3_Define 12  // Input Pin - HC celestial target selection (Star/Sun/Moon)
#define gpioPin_4_Define 11  // Control Pin - connected via 1k resistor to IO3

//PWM Pin:
#define pwmPin_Define 10     // PWM Output

//Status Pin:
#define statusPin_Define 13

//E-Stop Pin:
#define estopPin_Define 11   // Input Pin - float = normal, short to GND = EStop

//Motor Driver Pins:
#define resetPin_0_Define 55 //Analog 1
#define resetPin_1_Define 54 //Analog 0

#define dirPin_0_Define 3
#define dirPin_1_Define 7

#define enablePin_0_Define 4
#define enablePin_1_Define 8

#define stepPin_0_Define 5
#define stepPin_1_Define 12

#define modePins0_0_Define 15
#define modePins1_0_Define 16
#define modePins2_0_Define 17
#define modePins0_1_Define 20
#define modePins1_1_Define 19
#define modePins2_1_Define 18

//ST4 Pins:
#define ST4AddPin_0_Define 50
#define ST4AddPin_1_Define 51
#define ST4SubPin_0_Define 53
#define ST4SubPin_1_Define 52


//
//----- End User Configurable Pin Assignments -----
//


#elif defined(PIN_MAP_MKS_GEN_L)
//
//---- MKS Gen L and RAMPS 1.4 Pin Definitions -----
//

//GPIO Pins:
                             //VCC (Header Pin 5)
#define gpioPin_0_Define 49  //IO0 - GPIO Pin - EXP2 Pin 7 (Gen L) or Aux-3 Pin 2 (Ramps 1.4)  - connect to ST-4 pin 1
#define gpioPin_1_Define 33  //IO1 - GPIO Pin - EXP2 Pin 5 (Gen L) or Aux-4 Pin 11 (Ramps 1.4) - SNAP pin.
#define gpioPin_2_Define 41  //IO2 - GPIO Pin - EXP2 Pin 10 (Gen L) or Aux-4 Pin 7 (Ramps 1.4) - connect via 1k resistor to EXP2, Pin 7
                             //GND (Header Pin 1)

//PWM Pin:
#define pwmPin_Define 9      // FAN_PIN (Gen L only)

//Status Pins:
#define statusPin_Define 13       // LED_PIN (Gen L only)
#define statusPinShadow_Define 11 // Left servo header (Ramps 1.4 only) - connect to LED via suitable resistor. 

//E-Stop Pin:
#define estopPin_Define 18     // Z_MIN_PIN - Input Pin - float = normal, short to GND = EStop

//Motor Driver Pins:
#define resetPin_0_Define 35   // Unused on RAMPS
#define resetPin_1_Define 37   // Unused on RAMPS

#define dirPin_0_Define 55     // X_DIR_PIN
#define dirPin_1_Define 61     // Y_DIR_PIN

#define enablePin_0_Define 38  // X_ENABLE_PIN
#define enablePin_1_Define 56  // Y_ENABLE_PIN

#define stepPin_0_Define 54    // X_STEP_PIN
#define stepPin_1_Define 60    // Y_STEP_PIN

#define modePins0_0_Define 25
#define modePins1_0_Define 27
#define modePins2_0_Define 29
#define modePins0_1_Define 16
#define modePins1_1_Define 17
#define modePins2_1_Define 23

//ST4 Pins:
#define ST4AddPin_0_Define 50  //EXP2, Pin 1 (Gen L) or Aux-3 Pin 3 (Ramps 1.4) = RA+  - Connect to st-4 pin 6
#define ST4AddPin_1_Define 51  //EXP2, Pin 6 (Gen L) or Aux-3 Pin 4 (Ramps 1.4) = DC+  - Connect to st-4 pin 5
#define ST4SubPin_0_Define 53  //EXP2, Pin 4 (Gen L) or Aux-3 Pin 6 (Ramps 1.4) = RA-  - Connect to st-4 pin 3
#define ST4SubPin_1_Define 52  //EXP2, Pin 2 (Gen L) or Aux-3 Pin 5 (Ramps 1.4) = DC-  - Connect to st-4 pin 4
                               //EXP2, Pin 9 (Gen L) or Aux-3 Pin 7 (Ramps 1.4) = GND  - Connect to st-4 pin 2


//
//----- End MKS Gen L Pin Assignments -----
//


#elif defined(__AVR_ATmega162__)

//
//----- Pin Definitions for ATMega162 Variants -----
//Warning: D20 to D27 inclusive are NOT allowed

//GPIO Header:
                             //VCC (Header Pin 5)
#define gpioPin_0_Define 2   //IO0 (Header Pin 4) [ATMega PD2] - GPIO Pin - HC Detect/Speed
#define gpioPin_1_Define 29  //IO1 (Header Pin 3) [ATMega PE1] - Output Pin - General purpose output (EQMOD "SNAP" 1)
#define gpioPin_2_Define 28  //IO2 (Header Pin 2) [ATMega PE0] - Control Pin - connected via 1k resistor to IO0
                             //GND (Header Pin 1)
#define gpioPin_3_Define 12  //IO3 (PrgHdr Pin 1) [ATMega PB6] - Input Pin - HC celestial target selection (Star/Sun/Moon)
#define gpioPin_4_Define 20  //IO4 (MCU   Pin 21) [ATMega PC0] - Control Pin - connected via 1k resistor to IO3

//PWM Pin:
#define pwmPin_Define    9   // (PWM Jack) [ATMega PB1] - Open Drain Output
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

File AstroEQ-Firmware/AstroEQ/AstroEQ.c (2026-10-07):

/*
  Code written by Thomas Carpenter 2012-2017
  
  With thanks Chris over at the EQMOD Yahoo group for assisting decoding the Skywatcher protocol
  
  
  Equatorial mount tracking system for integration with EQMOD using the Skywatcher/Synta
  communication protocol.
 
  Works with EQ5, HEQ5, and EQ6 mounts, and also a great many custom mount configurations.
 
  Current Version: <see AstroEQ.h header>
*/

//Only works with ATmega162, and Arduino Mega boards (1280 and 2560)
#if defined(__AVR_ATmega162__) || defined(__AVR_ATmega1280__) || defined(__AVR_ATmega2560__)

/*
 * Include headers
 */
 
#include "AstroEQ.h" //AstroEQ header

#include "EEPROMReader.h" //Read config file
#include "SerialLink.h" //Serial Port
#include "UnionHelpers.h" //Union prototypes
#include "synta.h" //Synta Communications Protocol.
#include "commands.h" //Synta Communications Protocol.
#include <util/delay.h>    
#include <util/delay_basic.h>
#include <util/crc16.h>
#include <avr/wdt.h>
#include <avr/common.h>


// Watchdog disable on boot.
void wdt_init(void) __attribute__((naked)) __attribute__((section(".init3")));
void wdt_init(void)
{
    wdt_disable();
    return;
}

/*
 * Defines
 */

#define SET_PROG_MODE(newMode) progMode = (newMode); cmdIsProg = (progMode == RUNMODE) ? CMD_LEN_RUN : CMD_LEN_PROG

/*
 * Global Variables
 */
byte stepIncrement[2];
MotionStart readyToGo[2] = {MOTION_START_NOTREADY, MOTION_START_NOTREADY};
unsigned long gotoPosn[2] = {0UL,0UL}; //where to slew to
bool encodeDirection[2];
ExecMode progMode = RUNMODE; //MODES:  0 = Normal Ops (EQMOD). 1 = Validate EEPROM. 2 = Store to EEPROM. 3 = Rebuild EEPROM
CmdProgMode cmdIsProg = CMD_LEN_RUN;
byte progModeEntryCount = 0; //Must send 10 non-zero progMode commands to switch out of run-time. This is to prevent accidental entry by EQMOD.
byte microstepConf;
byte driverVersion;
bool standaloneMode = false; //Initially not in standalone mode (EQMOD mode)
bool syntaMode = true; //And Synta processing is enabled.
bool snapPinIsOpenDrain = false;

#define timerCountRate 8000000

#define DecimalDistnWidth 32
unsigned int timerOVF[2][DecimalDistnWidth];
bool canJumpToHighspeed = false;
bool defaultSpeedState = SPEEDNORM;
bool disableGearChange = false;
bool allowAdvancedHCDetection = false;
unsigned int gotoDecelerationLength[2];
byte accelTableRepeatsLeft[2] = {0,0};
byte accelTableIndex[2] = {0,0};

/*
 * Helper Macros
 */

//These should not be used directly. They are used for
//overloading of the register access macros to allow
//set and get operations to be performed using the same
//name.
#define GET_TERNARY_MACRO(m,_1,NAME,...) NAME
#define SET_TERNARY_REGISTER(rt,rf,m,c) if(m) {rt = c;} else {rf = c;}
#define GET_TERNARY_REGISTER(rt,rf,m)   ((m) ? rt : rf)
#define GET_SINGULAR_MACRO(_1,NAME,...) NAME
#define SET_SINGULAR_REGISTER(r,c) {r = c;}
#define GET_SINGULAR_REGISTER(r)   (r)

//Registers
//For setting an RA/DC register -> macro(RA,setValue)
//For getting an RA/DC register -> macro(DC)
#define distributionSegment(...)       GET_TERNARY_MACRO(__VA_ARGS__,  SET_TERNARY_REGISTER ,  GET_TERNARY_REGISTER )(GPIOR1,GPIOR2,__VA_ARGS__)
#define currentMotorSpeed(...)         GET_TERNARY_MACRO(__VA_ARGS__,  SET_TERNARY_REGISTER ,  GET_TERNARY_REGISTER )( OCR3A, OCR3B,__VA_ARGS__)
#define irqToNextStep(...)             GET_TERNARY_MACRO(__VA_ARGS__,  SET_TERNARY_REGISTER ,  GET_TERNARY_REGISTER )( OCR1A, OCR1B,__VA_ARGS__)
#define timerCountRegister(...)        GET_TERNARY_MACRO(__VA_ARGS__,  SET_TERNARY_REGISTER ,  GET_TERNARY_REGISTER )( TCNT3, TCNT1,__VA_ARGS__)
#define timerPrescalarRegister(...)    GET_TERNARY_MACRO(__VA_ARGS__,  SET_TERNARY_REGISTER ,  GET_TERNARY_REGISTER )(TCCR3B,TCCR1B,__VA_ARGS__)
#define interruptOVFCount(...)         GET_TERNARY_MACRO(__VA_ARGS__,  SET_TERNARY_REGISTER ,  GET_TERNARY_REGISTER )(  ICR3,  ICR1,__VA_ARGS__)
#define interruptControlRegister(...)  GET_TERNARY_MACRO(__VA_ARGS__,  SET_TERNARY_REGISTER ,  GET_TERNARY_REGISTER )(TIMSK3,TIMSK1,__VA_ARGS__)
#define polarscopeDutyRegister(...)   GET_SINGULAR_MACRO(__VA_ARGS__, SET_SINGULAR_REGISTER , GET_SINGULAR_REGISTER )(        OCR2A,__VA_ARGS__)
#define gotoControlRegister GPIOR0
//Bit Masks
#define interruptControlBitMask(m)  (m ? _BV(ICIE3) : _BV(ICIE1))
#define gotoDeceleratingBitMask(m)  (m ? _BV(    3) : _BV(    2))
#define gotoRunningBitMask(m)       (m ? _BV(    1) : _BV(    0))





/*
 * Inline functions
 */
inline bool gotoRunning(const byte axis) {
    return (gotoControlRegister & gotoRunningBitMask(axis));
}
inline bool gotoDecelerating(const byte axis) {
    return (gotoControlRegister & gotoDeceleratingBitMask(axis));
}
inline void setGotoRunning(const byte axis) {
    gotoControlRegister |= gotoRunningBitMask(axis);
}
inline void clearGotoRunning(const byte axis) {
    gotoControlRegister &= ~gotoRunningBitMask(axis);
}
inline void setGotoDecelerating(const byte axis) {
    gotoControlRegister |= gotoDeceleratingBitMask(axis);
}
inline void clearGotoDecelerating(const byte axis) {
    gotoControlRegister &= ~gotoDeceleratingBitMask(axis);
}
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

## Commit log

2012-02-29 Initial commit of project. Currently tracking is at incorrect speed, I'm working on it :S
2012-04-22 Commit includes hardware schematics for Eagle 6.0
    [AstroEQ.brd, AstroEQ.sch, HTSSOP to DIL.brd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]
2012-04-23 Fixed bug with motor control with user chosen bValues.
2012-06-30 Version 5 Release.
    [Initialisation Variable Calculator.xlsx, SyncScan Standalone MK3 PTH.brd, SyncScan Standalone MK3 PTH.sch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]
2012-11-12 Added support for mounts with different gear ratio on each axis. For those with the same gear ratio on each mount, this update doesn't affect you.
    [Initialisation Variable Calculator.xlsx]
2012-12-08 Added support for changing goto speed. Also added support for using the Pololu A4983 board rather than the DRV8824 chips.
    [Initialisation Variable Calculator.xlsx]
2013-01-12 Restructure of AstroEQ repo prior to new release
    [AstroEQ.brd, AstroEQ.sch, HTSSOP to DIL.brd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]
2013-01-20 Software Update and new Hardware Designs
    Older hardware designs have been removed, and the repository cleaned up.
    The License file has also been updated.
    [AstroEQ DIY Etch.brd, AstroEQ DIY Etch.sch, AstroEQ PTH MK2.brd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]
2013-01-21 Added SMD design to fit inside EQ5 mount shell.
    [AstroEQ SMD MK2 (EQ5).brd, AstroEQ SMD MK2 (EQ5).sch, Google Sketchup 8 Rendering.skp]
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2013-05-28 New AstroEQ Version
    AstroEQ6 has been released and is better than ever!
    [AstroEQ PTH MK2.brd, AstroEQ PTH MK2.sch, Initialisation Variable Calculator.xlsx]
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2013-06-23 Added AstroEQ Kit assembly pictures
    Split the zip archive from my previous commit into smaller chunks as
    12MB is too big to download.
2013-06-24 Corrected glitch in Config utility
    Mount would not be programmed if there was a space in the filename. Also
    font on XP was rendered incorrectly.
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2013-07-13 Minor correction to last commit
    There was a minor bug in the goto speed settings which could cause short
    goto's to move at the wrong speed.
    [AstroEQ6.ino]
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2013-09-30 AstroEQ 6.3 Release (critical)
    6.3 fixes a glitch which causes the mount to not decelerate under EQMOD
    Rate Limiting. Everyone is advised to update to this version.
    [AstroEQ6.ino]
2013-09-30 AstroEQ 6.3 Release (critical)
    Also included is a never version of the Config utility which can now
    check for new firmware versions.
    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
2013-11-10 Firmware 6.5 Release
    New & improved acceleration and deceleration routines. Fixed PHD Guiding
    issues. Please download new config utility as this was also patched!
    [AstroEQ6.ino]
2013-12-14 Updated Configuration Utility
    Reduces the likely hood of the utility failing to read or write to the
    EEPROM (stalls at :G110). If this does still occur, simply try again,
    you shouldn't have to unplug or power off the controller!
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2014-01-12 AstroEQ Software V6.8 and Hardware V4.3
    S-V6.8: Faster processing of Serial commands for better guiding
    responsiveness. You can use the config utility to fetch the new
    firmware.
    H-V4.3: Minor PCB rearrangement to make soldering and assembly easier.
    Nothing changed electrically.
    [AstroEQ DIY Etch.brd, AstroEQ DIY Etch.sch, AstroEQ PTH MK2.brd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]
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2014-06-23 Fixes #14 Upload Issues for Mega2560
    There was a glitch in the configuration utility which meant it failed to
    upload firmware for the Arduino Mega2560 and Mega1280 boards. This is
    fixed.
2015-03-01 Update DIY Eagle Designs
    (1) Bring AstroEQ-DIY up to date (V4.4)
    (2) Export AstroEQ-DIY schematic to PDF
    (3) Make sure the etch file doesn't have holes in pads
    (4) Add AstroEQ-ARD variant - Arduino Mega sheild
    [AstroEQ Arduino Mega.brd, AstroEQ Arduino Mega.sch, AstroEQ DIY Etch.brd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]
2015-03-01 Correct Arduino Shield Etch PDF
    PDF for copper etch was missing Polygon layer.
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2015-05-07 Correct Board-Schematic Inconsistencies
    In the SMD design, the board and schematic files in Eagle had become
    inconsistent. This has been corrected.
    [AstroEQ SMD MK2 (EQ5).brd, AstroEQ SMD MK2 (EQ5).sch]
2015-05-23 AstroEQ 7.4 and Updated Config Utility
    Minor firmware improvements - AstroEQ 7.4.
    A new configuration utility which allows a wider range of mount ratios -
    this will allow configurations that previously got an IVal too small
    error. Also added the ability to test if a configuration will work
    without having to have an AstroEQ physically present.
    [AstroEQ.h, PinMappings.h]
2015-06-08 Update PCB Logo
    Add AstroEQ logo to PCB hardware designs.
    [AstroEQ Arduino Mega.brd, AstroEQ Arduino Mega.sch, AstroEQ DIY Etch.brd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]
2015-06-09 Correct Silk on PTH Gerbers
    Correct the Gerber files for the AstroEQ PTH version to have the correct
    silk layers included.
2015-12-31 Correct Schematic Labelling
    Correct labelling in schematic and add additional information to avoid confusion with pin assignments on driver boards.
    [AstroEQ Arduino Mega.sch, AstroEQ DIY Etch.sch, AstroEQ PTH MK3.sch]
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2016-02-01 Correct code indenting
    Correct the code indenting so that it uses the standard 4 spaces per tab
    rather than the Arduino IDEs nonsense choice of 2 spaces per tab. This
    makes editing the code in things like Notepad++ or UECIDE much easier.
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2016-02-01 Update AstroEQ Header File
    Update the AstroEQ header file.
    (1) Correct version number
    (2) Add new #defines for motor driver constants and pin direction
    constants
    (3) Update function prototypes changed in AstroEQ.cpp. Remove go-to
    deceleration parameter from motor start functions. Also change the
    driverVersion parameter to the mode mapping function to be a byte not a
    bool so that there can now be 3 different drivers.
    [AstroEQ.h]
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2016-02-21 Fix ST4 Pin Direction (URGENT!)
    The ST4 pin directions were misakenly set to be as outputs when updating
    the firmware for the v7.5 developments. This has been corrected. If you
    are using a version without this fix, make sure to apply it before using
    the ST4 port!
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2017-02-12 Update Hardware Files
    Update the repository to contain the latest hardware designs for AstroEQ
    V4.6, along with exported BOM.
    [AstroEQ PTH MK3.brd, AstroEQ PTH MK3.sch, AstroEQ V4.6 BOM.xlsx]
2017-02-25 Update AstroEQ DIY Design
    The DIY version of the design (intended for home-etching on single-sided
    PCB) was still V4.4. I have updated it to the V4.6 hardware.
    [AstroEQ DIY Etch.brd, AstroEQ DIY Etch.sch]
2017-02-25 Rename AstroEQ PTH PCB Filenames
    The AstroEQ Eagle files for the PTH design were still using an archaic
    version number (MK3) which predates the current hardware numbering. I
    have updated the eagle files to the correct version number to avoid
    confusion.
    [AstroEQ PTH MK3.brd, AstroEQ PTH MK3.sch, AstroEQ PTH V4.6.brd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]
2017-02-25 New AstroEQ Hardware Version (V4.7)
    This new version is designed for machine assembly by using a mixture of
    SMD and PTH components. The board is functionally identical to V4.6
    which will remain the version being used for blank PCBs. I recommend
    anyone doing DIY to use the V4.6 hardware.
    Additionally I have updating my SMD EQ5 design to the V4.7 hardware
    version. It was previously a V4.0 design. The upgrade is purely because
    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
    [AstroEQ PTH V4.7.brd, AstroEQ PTH V4.7.sch, AstroEQ SMD MK2 (EQ5).brd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]
2017-04-09 Update Hardware Designs
    Minor corrections to part attributes and some components in the V4.7
    design moved slightly to avoid collisions as found during the prototype
    build.
    [AstroEQ PTH V4.7.brd, AstroEQ PTH V4.7.sch, AstroEQ SMD V4.7 (EQ5).brd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]
2017-04-09 Minor improvements to Firmware files
    1. Add blocking flush command to SerialLink to allow all data in the TX
    buffer to be sent. This prevents response data from being lost when the
    controller is reset during configuration.
    2. Clean up of constants in Synta.cpp
    3. Remove superfluous/incorrect comment from PinMappings.h
    [PinMappings.h]
2017-04-09 Major Firmware Improvements
    1. Tidy up commands.h and commands.cpp to correct some indentation and
    improve readability.
    2. Add new ST-4 speed constant to firmware. This allows ST4 factor to be
    changed through the configuration utility
    3. Rename st4Pin to st4Pins as it is an array of all ST4 pins.
    4. Rewrite whole ST-4 processing. Remove the pin change interrupt that
    was driving ST-4 and instead use a polling approach in the main()
    function. This allows for better resiliance to bounce of the inputs and
    prevents the controller from missing the end of an ST4 pulse and not
    stopping.
    5. Bump version number in code which was still saying 7.5
    6. Complete basic handcontroller mode, including a new r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
    [AstroEQ.h, EEPROMAddresses.h]
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2017-06-26 Update AstroEQ Atmel Studio Solution/Project Files
    Add project files for the Arduino Mega 2560 and 1280. These use the same
    source code, but seperate projects are needed to ensure the correct MCU
    is set and the custom programming tool strings are correct.
    Additionally a post build even has been added to all projects which will
    automatically copy the release firmware file into the AstroEQ Config
    Utility Hex files folder in the main repository. It will also update the
    version number in the versions.txt file based on the VerNum.txt file in
    the firmware folder.
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2017-07-02 Update Displayed Firmware Version When Fetching New Firmware
    The firmware version shown by the drop down menu was not being updated
    after a new firmware version is downloaded. This is fixed now. For
    longer version numbers (e.g. 8.03) the number was getting cut off, so
    more space has been made available for the number to be displayed in.
    [AstroEQUploader.pde, UploaderGUI.pde]
2017-07-06 Bump Version + Recompile
    Recompile with the corrected flags for signed chars. Also bump version
    number to 8.04.
    The new firmware is available by using the "Check for New Firmware"
    button in the config utility.
    [AstroEQ.c, AstroEQ.h]
2017-07-15 Fix Spelling/Typos in main.c Comments
    A bit more copy editing. No code changes, just comments.
    [AstroEQ.c]
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2017-07-18 Fix Atmel Studio Solution Settings
    The solution settings for the AstroEQ project were wrong which was
    resulting in every version of the firmware being compiled for ATMega162
    - even the Arduino Mega projects.
    To solve this each project in the solution requires its own
    configuration name to keep intermediate files from getting shared
    between different processors.
    This is the root cause of issue #20.
2017-07-18 Fix Serial_flush() function
    The implementation of flush was completely backwards - it was waiting
    for the buffer to fill not drain.
    [SerialLink.c]
2017-07-18 Fix Header Text
    In the AstroEQ.h file refer people to VerNum.txt to get current version
    number.
    [AstroEQ.h]
2017-09-02 Patch Config Utility to Use "avrdude" Package (Fixes #22)
    This is a fix to issue #22 in which the distributed i386 version of
    avrdude was not functional on other platforms such as amd64 or armhf.
    This patch changes the directories of the avrdude files in linux to
    point to those included with the avrdude package which will already be
    of the correct architecture to match os.
    [AstroEQUploader.pde]
2017-09-03 Fix Regression in Linux Version
    Accidentially caused Linux version on some computers to print larger
    numbers of window size messages to the log window.
    [AstroEQUploader.pde]
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2017-10-16 Change Configuration Structure (CRC + Vernum)
    NOTE: Changes require new config utility. Will follow.
    Change the header for the configuration structure. The new header uses a
    shortened ID string (AEQ rather than AstroEQ). The freed bytes now
    contain a version number string and a CRC8-CITT word.
    The CRC and version number will aid in future changes to the
    configuration structure.
    Additionally these changes make updating from older versions (pre 8.0)
    possible. Previously the firmware was crashing because of major changes
    made to the configuration structure in 8.0. That issue is resolved.
    [AstroEQ.c, AstroEQ.h, EEPROMAddresses.h]
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2017-10-18 Fix Mistake in DEC Timer Initialisation
    The DEC timer was not being initialised to the correct value. This
    probably won't have caused any issue as both DEC and RA use same values
    for unused control bits anyway.
    [AstroEQ.c]
2017-10-19 Correct handling of Mount Status :f command
    Errm, yeah. Somehow for the last 5 years the AstroEQ has worked with
    this error....
    Bascially the bits in the :f response were muddled up so that it was
    reporting "stopped/!running" instead of "slew/!goto", and "goto/!slew"
    instead of "running/!stopped". Because of the inversion of the bits as
    well as them being swapped, EQMOD managed to cope OK it seems. INDIlib
    on the other hand was getting upset and doing strange things (and
    rightfully so!)...
    Anyway, this major WTF moment has been resolved. I've also added in a
    missing highspeed/lowspeed flag to help INDI understand what is going on
    internally. EQMOD doesn't use this flag, but no harm it bein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
2018-01-03 Correct Arduino Mega Pin Mapping SPI pins
    Correct the #defines for the SPI pins to link them with the ST4 pins as
    they should be.
    [PinMappings.h]
2018-02-03 Add Bootloader Fuse Information
    Add information about ATMega162 bootloader fuses for use with
    MicrochipDirect.
    [ATMEGA162.xlsx]
2018-02-03 Correct Minor Glitches in Config Utility
    Correct some minor glitches in the configuration utility.
    [AstroEQUploader.pde, GUIScreen.pde, UploaderGUI.pde]
2018-02-19 Correct Config Utility Bug
    There was a bug in the config utility which meant some perfectly valid
    configurations were coming up as "IVal too large" even though there was
    a suitably small value that would work fine.
    [AstroEQUploader.pde, UploaderGUI.pde]
2018-04-12 Fix Typo in Config Utility
    Config, not confing. Woops.
    [UploaderGUI.pde]
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2018-06-23 Change Programming Mode Entry Strategy (Issue #24)
    Since EQMOD V2.00, the :Oxx is issued as part of run time. This caused AstroEQ to spuriously enter programming mode causing connection issues.
    To combat the problem, programming mode entry now requires 20 successive :O1x commands with no other commands in between.
    It is highly unlikely EQMOD will ever issue this many :O1x commands without other commands interleaved. EQMOD always appears to send :O1x commands together with a companion :O2x command. This is enough to prevent entry as only an :O1x command is considered.
    [AstroEQ.c, Executioner.pde]
2018-06-23 Add :V2xx Handling for PWM Output
    EQMOD since V2.00 can now issue polarscope brightness commands using :V2xx.
    Since AstroEQ hardware V4.6, a PWM output has been included for driving a polarscope LED, but up until now there has been no way of controlling it.
    Handling of the :V command has now been included to finally allow control of the polar scope LED output.
    [AstroEQ.c, AstroEQ.h, PinMappings.h]
2018-06-23 Improve :O2x Handling
    The purpose of EQMOD using the :Oxx command has become clearer. This is used to control up to two GPIO pins, for example to trigger a camera shutter.
    The :O1x command in AstroEQ is used to enter programming mode, so in order to tell EQMOD not to use the SNAP1 interface, AstroEQ now reports an error packet when :O1x is issued in run-mode. The configuration utility knows to expect this error packet. On the 20th time of writing :O1x, AstroEQ enters programming mode and sends a success packet.
    This should provide a secure way of fixing issue #24.
    AstroEQ V4.6 and newer, as well as Mega variants, have a spare GPIO pin not used for standalone mode. To still allow a feature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
    [AstroEQ.c, AstroEQ.h, Executioner.pde]
2018-06-23 Correct Programming Mode Entry Count
    The final :O1x command (i.e. when entry count == 19) should be handled as an actual entry command. The limit in the code was applied wrongly.
    [AstroEQ.c]
2018-06-23 Swap :O2x and :O1x
    EQMOD will not find the SNAP2 feature if the SNAP1 feature is unavailable.
    As such I have swapped around :O2x and :O1x. AstroEQ now uses :O1x for the SNAP1 feature, and :O2x for entering programming mode.
    This change won't prevent the config utility talking to old versions of the firmware, as originally both :O1x and :O2x could be used for entering config mode.
    The configuration utility has been updated to issue :O2x commands.
    [AstroEQ.c, Executioner.pde, UploaderGUI.pde]
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2018-09-01 Update AstroEQ.c
    Fix motorStop functions resetting GVal to slew mode
    [AstroEQ.c]
2018-09-01 Possible fix to Indilib-GVal Handling
    In some rare cases, :f commands are sent from indilib after updating the :GVal, but before initialising a movement.
    AstroEQ doesn't normally update its high-speed gear flag until a movement starts, which can confuse indilib into thinking high-speed wasn't supported (I think?).
    Anyway, this fix allows the :G command to update the high speed flag immediately if the motors aren't running.
    [AstroEQ.c, AstroEQ.h]
2018-09-02 Only reset GVal on motor stop if in GOTO mode
    [AstroEQ.c]
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2019-01-08 Add Duplicate Status LED Option
    Add the ability in pin mappings to map the status LED to two pins. This is primarily intended for the RAMPS1.4/MKSGenL variant where the MKS Gen L doesn't have a status LED on pin 13.
    [AstroEQ.c, AstroEQ.h, PinMappings.h]
2019-02-26 Ensure Motor Flags Clear on Reconnect
    If reconnecting the mount after it has previously been running, there can be a race condition where the motor running flag doesn't get cleared.
    This is now cleared whenever motors are enabled.
    [AstroEQ.c]
2019-03-13 Add Emergency Stop Input
    Add handling code for an e-stop input that when pulled low will cause the mount to stop moving and prevent further movements until released.
    On the ATMega162 based AstroEQ devices, this will be the MISO pin on the ISP header.
    [AstroEQ.c, AstroEQ.h, PinMappings.h]
2019-03-13 Add Config Option For GPIO1 Output Type
    Allow the "Snap" pin (GPIO) to be configured as either push-pull or open-drain.
    [AstroEQ.c, AstroEQUploader.pde, EEPROMAddresses.h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]
2020-01-17 Fixed a bug where not all commands were sent and another problem where GearChange was not used after selecting another uSteps value
    [UploaderGUI.pde]
2020-01-18 Swap Upload Firmware and Configure Button Positions
    Upload Firmware is really the first step for first users so it should appear first.
    [UploaderGUI.pde]
2020-05-05 Correct Corrupt EEPROM Recovery Mode
    When upgrading from a very old version of the firmware, or if the EEPROM gets corrupted, the AstroEQ goes into a recovery mode.
    However this recovery mode was not working with the configuration utility as intended, resulting in a timeout.
    This fix corrects the entry into programming mode.
    [AstroEQ.c]
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2020-07-14 Fix Issue #31 - Config Utility with Java 14
    Windows
    1. Update to launch4j v3.12 when packaging the utility as an EXE. This correct java detection for versions newer than Java 9 (due to change in version number format).
    2. Fix EXE path detection for Java 11 and newer
    3. Update JSSC native libraries including the addition of a 64 bit library to allow 64bit JRE to be used.
    Ubuntu:
    1. Correct Java version check to cope with version numbers changing from 1.x.0 to x.0.0.
    2. Ensure JSSC native library location is on the java library path to avoid issues with it not linking
    [AstroEQUploader.pde]
2020-07-15 Update Readme Version Number
    Config v3.9.3 was just released to fix issues with newer versions of Java.
    Software 8.18 was released a couple of months ago to fix an issue with recovery mode.
2021-01-08 Fix :J Handling for GS Server
    The GS Server software issues a :J command after the :I command, even when updating the speed. Indilib doesn't issue the extra :J command. EQMOD always issues a :K anyway so this is irrelevant.
    In order to support GS Server, we must ignore this extra :J command if we have updated the speed, to avoid the state machine controlling movement start from locking up.
    [AstroEQ.c]
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2022-12-11 All Different cmd Payload/Response Lengths in Prog
    So the command set has been extended in the skywatcher documentation, which is now causing problems because I use some of the commands for my own purpose in programming mode. For now it is just the 'q' command which requires a different payload length in the protocol than I use.
    To solve this, we now have the ability to set different lengths for programming mode and run mode commands by using the upper nibble of the payload length parameter which was always zero before.
    [AstroEQ.c, synta.c]
2022-12-11 Add :q command handling for Run Mode
    No idea if this is correct, the protocol documentation is hellishly unclear.
    [AstroEQ.c]
2022-12-11 Add Error Code Handling
    The synta protocol allows an error code to be sent back with the ! response.
    [AstroEQ.c, synta.c]
2024-02-04 Fix Error Responses for Programming Mode
    Don't use error codes in programming mode as the config utility is not set up to handle them. Otherwise it fails to detect communication errors or blank EEPROMs causing the AstroEQ to fail to boot.
    [synta.c]
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2024-09-01 Correct Changes to Synta Hex<->Nibble Functions
    Managed to turn 'A'-10 into just 'A' somewhere along the way. Meant that A-F were turning into 0-5 instead of 10-15.
    [synta.c]
2024-09-01 Correct Conversion to Enum for MotorRunning
    Accidentally inverted the meaning of Stopped/Running.
    [AstroEQ.c]
2024-09-01 Send error response to unknown commands.
    The unknown commands should have been generating an error response, but were not due to a missing else statement.
    [AstroEQ.c]
2026-01-22 Ensure :J is not treated as an unknown command in run mode
    The new error reporting accidentally made :J and unknown command preventing mount operations from being performed.
    [AstroEQ.c]
2026-01-22 Add Lunar/Solar ST4 Mode Options
    When selected, these scale the sidereal IVal to approximate the equivalent Lunar or Solar IVal to within a reasonable margin of error and use the calculated value as the base speed for ST4 movements.
    [AstroEQ.h]
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2026-01-22 Add IO3 Sidereal/Lunar/Solar Tracking Selection Switch
    Requires 1k resistor to be connected from IO0 to IO3.
    * Short IO3 to GND = Lunar speed
    * Pull IO3 to GND with 3.9k resistor = Solar speed
    * Float IO3 = Sidereal speed
    This is the same switch design as the basic hand-controller shown in https://www.astroeq.co.uk/forum/index.php/topic,190.0.html
    [AstroEQ.c]
2026-01-22 Redesign Lunar/Solar/Sidereal speed selection approach
    There was a fundamental flaw in the addition of the new sidereal speed. It essentially boils down to the fact that we cannot use the same pull-up resistor to do ternary state detection on more than one pin.
    Because there are no more spare pins on ATMega162 variant, we can't have the tracking speed selection be a ternary state input, only a simply high-low input.
    Instead, we now use the same speed selection switch that selects Sidereal/2x/GoTo rate for both. When the new target speed input switch is high, it will maintain the old behaviour. When the new input is low, it remaps the speed selection switch to instead by Sidereal/Solar/Luna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
    [AstroEQ.c, PinMappings.h]
2026-01-30 Use ST4 RA Tracking IVal for standalone HC when returning to tracking
    This contains the correct IVal for the currently selected tracking mode (Sidereal/Lunar/Solar).
    [AstroEQ.c]

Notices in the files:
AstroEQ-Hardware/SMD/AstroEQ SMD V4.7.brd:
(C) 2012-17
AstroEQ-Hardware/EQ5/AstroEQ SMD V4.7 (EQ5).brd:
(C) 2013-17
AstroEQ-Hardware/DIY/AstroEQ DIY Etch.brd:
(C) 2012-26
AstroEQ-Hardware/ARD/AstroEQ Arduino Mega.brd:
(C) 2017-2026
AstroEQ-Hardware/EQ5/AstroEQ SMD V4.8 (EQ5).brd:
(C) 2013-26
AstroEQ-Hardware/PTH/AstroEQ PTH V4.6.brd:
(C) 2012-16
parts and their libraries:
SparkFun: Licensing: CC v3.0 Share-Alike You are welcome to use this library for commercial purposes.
